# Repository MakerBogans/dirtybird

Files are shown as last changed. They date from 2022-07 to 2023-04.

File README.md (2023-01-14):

# The DirtyBird toolhead

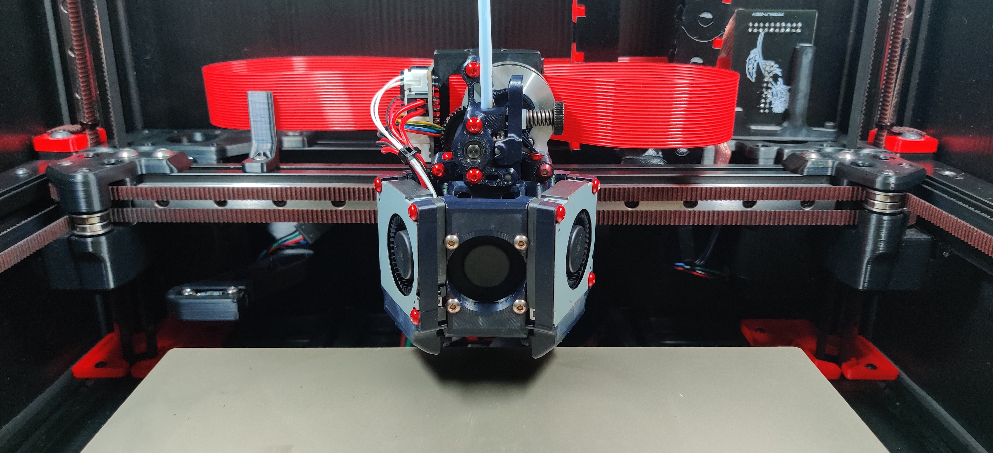
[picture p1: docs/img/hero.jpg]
DirtyBird Toolhead


Developed as the successor of the Frankensherpa toolhead.

Like its predecessor, DirtyBird is designed to:

- Be lightweight, allowing greater acceleration and potentially improved resonance
- Have excellent cooling performance, with dual blower fans to improve overhang performance with many materials (including PLA)
- Have fans that are mounted low on the toolhead (cf. Afterburner) to improve resonance
- Allow for easy maintenance of the extruder
- Use a simplified carriage with integrated magprobe support
- Remain compatible with stock Voron (and Ramalama) idlers
- Support Roadkill-based chainless toolhead boards

Currently, DirtyBird supports the following extruders (and more via usermods):

- LGX mini
- Sherpa mini
- Sherpa micro

And the following hotends:

- Dragon
- NF Crazy
- Rapido (HF only, UHF not supported yet)

### BOM

[See BOM](./docs//bill-of-materials.md)

### Build Instructions

[See Build Instructions](./docs/build.md)

### Planned features

- MGN9 support (currently, the carriage fits MGN12 rails only)
- Filament sensor support (for Enraged Rabbit Carrot Feeder or other multi-material operation, under development)
- Integrated LED lighting (using Neopixels, currently experimental)
- Rapido hotend support (currently experimental)
- Cable chain mount (?)

### Known issues/to do list

- Potentially insufficient clearance between the Dragon core and the heater block of the Dragon hotend; as a result, the core may melt or otherwise cook, especially when using a silicone sock
  - Improvements have been made, but we are gathering feedback from real world usage.
- Rename files for version control/clarity (i.e. similar to Annex)
- Printed L/R marks for the fan ducts

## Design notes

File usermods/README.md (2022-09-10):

Contains usermods for the DirtyBird toolhead.

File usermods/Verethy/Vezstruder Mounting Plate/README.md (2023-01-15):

# Mod description

**Vz-Hextrudort Mounting Plate**

Mounting plate the attach the Vz-Hextrudort extruders.

Veztruder

# Status

Release

# Incompatibilities

None

# Update notes

2x M3x6 BHCS to secure from the bottom.

# Instructions

**Print settings**

The STL is correctly oriented, do not change orientation

**Additional hardware**

2x M3x6 BHCS

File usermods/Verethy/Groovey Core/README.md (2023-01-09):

# Mod description

**Groovey Core**

Adds a new core to allow groove mount hotends to be mounted to the DB

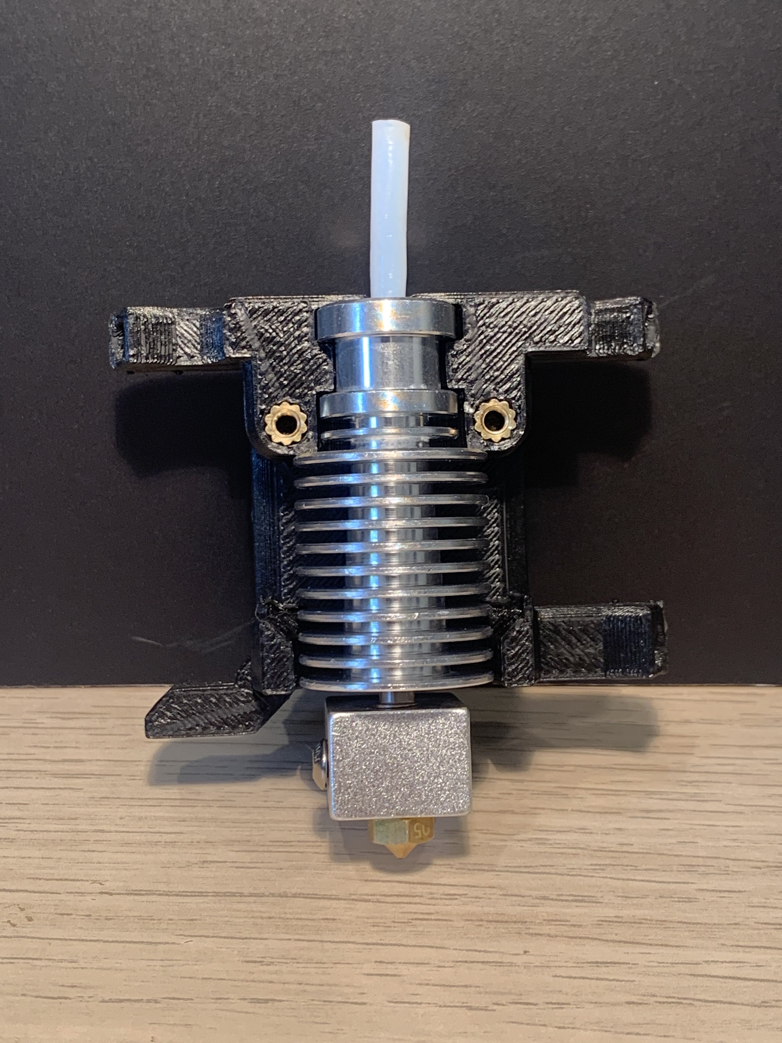
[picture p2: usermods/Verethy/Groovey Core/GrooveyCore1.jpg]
Groovey core

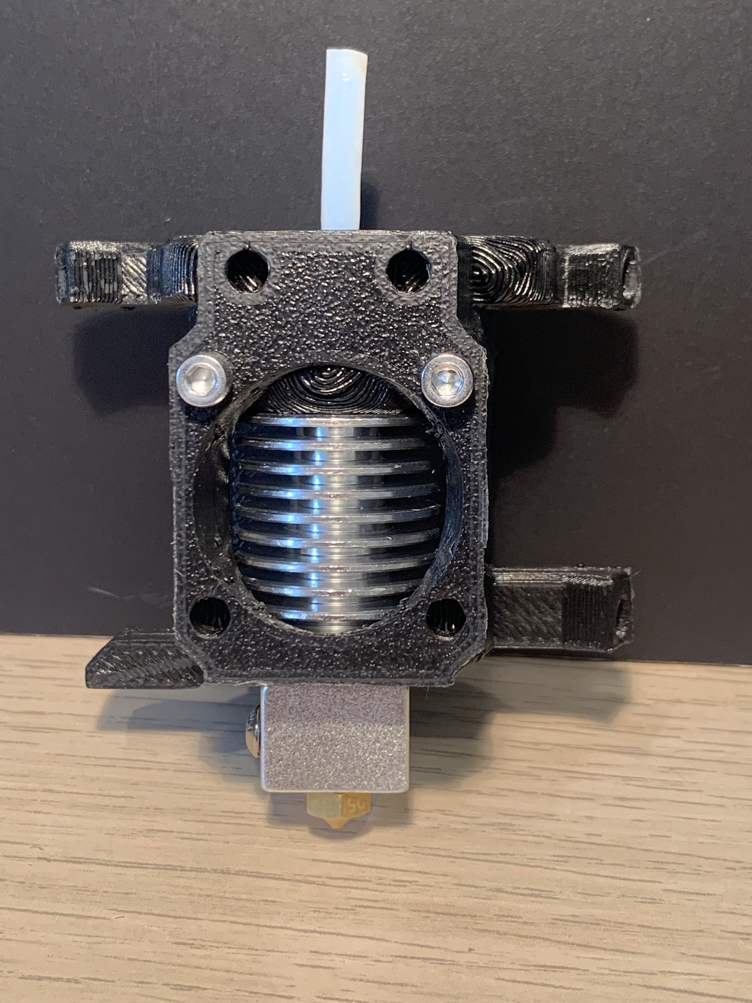
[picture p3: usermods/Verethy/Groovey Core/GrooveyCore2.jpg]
Groovey core

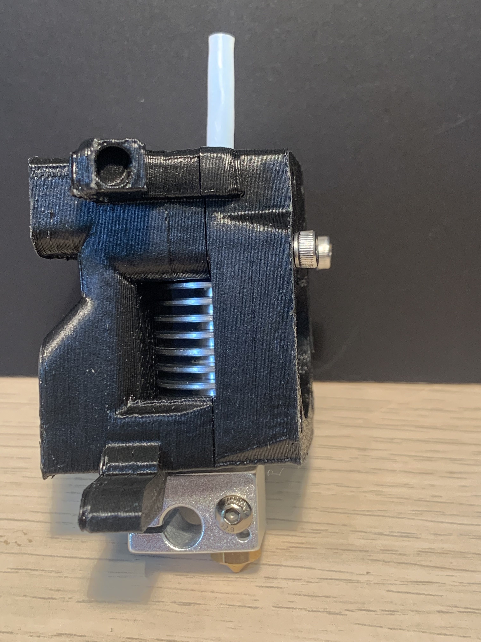
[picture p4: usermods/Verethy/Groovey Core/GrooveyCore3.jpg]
Groovey core


# Status

Release

# Incompatibilities

Sherpa Micro

# Update notes

Compatible with Dragon/Crazy ducts.
Replace the top 2 hotend fan screws with 2 M3x35mm BHCS

# Instructions

**Print settings**

The STL is correctly oriented, do not change orientation

**Additional hardware**

2x M3x35 BHCS

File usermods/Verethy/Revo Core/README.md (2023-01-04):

# Mod description

**Revo Core**

Adds a new core to allow Revo hotends to be mounted to the DB

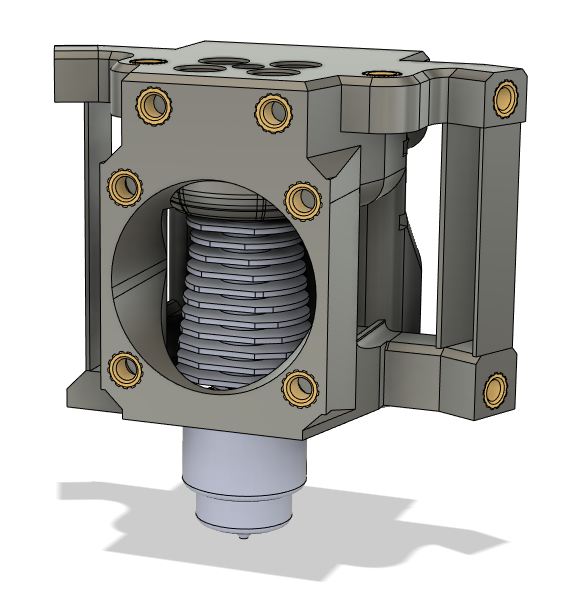
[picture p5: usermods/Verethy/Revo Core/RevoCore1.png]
Revo core


# Status

Release

# Incompatibilities

None

# Update notes

Compatible with Dragon/Crazy ducts.
Bowden length: 22.4 to top of core.

# Instructions

**Print settings**

The STL is correctly oriented, do not change orientation

**Additional hardware**

4x M3x8 SHCS

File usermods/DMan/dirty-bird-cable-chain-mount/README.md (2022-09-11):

# Dirty Bird Cable Chain Mount

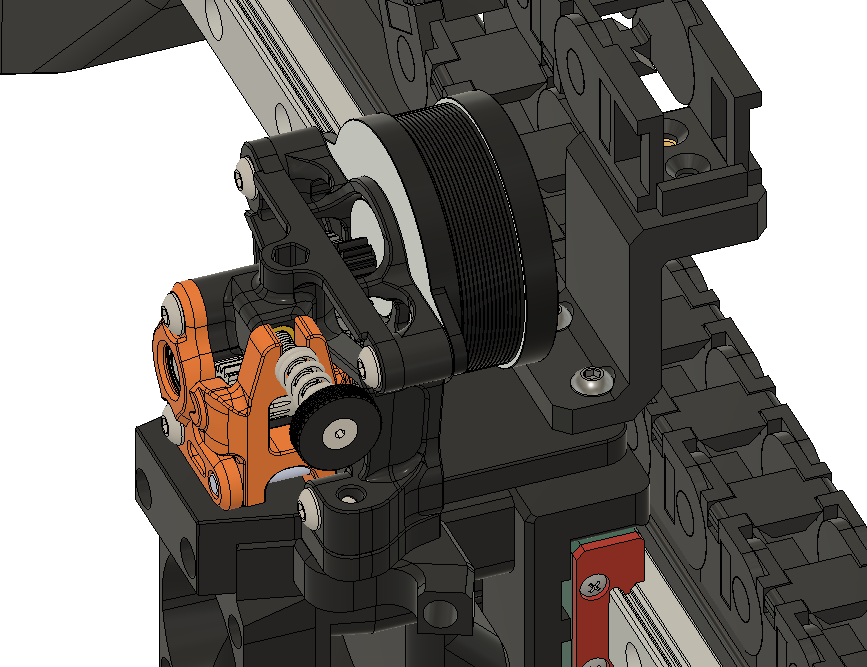
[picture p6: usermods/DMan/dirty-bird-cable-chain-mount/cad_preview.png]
Cable Chain Mount


## Status

I've got this on my V2.4 350 mm, and it works well!

## How to

Print on its side, no supports. 3x M3 inserts and BHCS screws to hold the chain in place, and 2x M3x12 BHCS/SHCS to hold the mount to the X carriage.

Note I'm using the Mini Sherpa mount. You might need to adjust the height by 4 mm if you are not using this little adapter!

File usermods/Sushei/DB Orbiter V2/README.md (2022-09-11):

Please note:
This mount cannot be used with the roadkill long PCB.

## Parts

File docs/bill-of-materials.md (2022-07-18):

# DirtyBird BOM

Exact fastener counts may differ slightly based on your configuration.

Purchasing spares is highly recommended.

For other projects that are used in DirtyBird (e.g. Klicky probe) refer to their respective documentation pages for an up-to-date BOM.

### Essential Fasteners

| Item | Quantity | Notes |
| :---: | :---: | :---: |
| Brass M3x4x5 Threaded Inserts | 20 | |
| M3x8 SHCS | 4 | |
| M3x12 SHCS | 3 | |
| M3x14 SHCS | 4 | |
| M3x16 SHCS | 3 | |
| M3x20 SHCS | 8 | |
| M3x6 BHCS | 2 | |
| M3x12 BHCS | 6 | |
| M3x20 BHCS | 4 | |
| M2.5 SHCS | 4 | Mounting bolts for your hotend (e.g. 10 mm bolts for Dragon hotends) |
| M3 SHCS/BHCS | 2 |  Mounting bolts for your extruder (e.g. M3x10 SHCS for Sherpa mini)  |

_BHCS button-head cap screw, SHCS socket-head cap screw_

### Fans

| Item | Quantity | Notes |
| :---: | :---: | :---: |
| Delta 4510 Blower Fan (BFB04512HHA-C) | 2 | |
| 3010 Hotend Cooling Fan | 1 | Airflow must be higher than 4 CFM |

### Other

| Item | Quantity | Notes |
| :---: | :---: | :---: |
| Extruder | 1 | Sherpa Mini, Sherpa Micro and LGX lite are currently supported |
| Hotend | 1 | Dragon & NF Crazy currently supported. Rapido support planned  |
| Bed Levelling Probe | 1 | Native support for Klicky. Euclid support in UserMod. |
| 6x3 Magnet | 3 | For Klicky mounting |
| 4mm OD, 2mm ID PTFE | 10cm | PTFE Liner between Extruder & Hotend |

### Optional Items

| Item | Quantity | Notes |
| :---: | :---: | :---: |
| Roadkill Longboi | 1 | Another board is recommended for terminating the ribbon cable, see Roadkill documentation for details |
| Roadkill Square | 1 | Support in UserMod. |
| Neopixel 5050 LEDs (on a 12.5mm diameter PCB) | 2 | TBC |
| Omron D2F Microswitch | 1 | For X endstop |

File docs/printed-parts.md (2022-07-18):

# DirtyBird Printed Parts

### Carriage

| Item | Filename | Notes |
| :---: | :---: | :---: |
| Klicky probe | Dirty Bird Klicky Carriage20 | |

### Hotend

Affects core and duct selection. Choose one set of files.

| Item | Filename | Notes |
| :---: | :---: | :---: |
|  Dragon  | DB Dragon Core | Available as two files (with or without supports) |
| |  Dragon Left Duct | |
| |  Dragon Right Duct  | |
| NF Crazy | DB Crazy Core | Available as two files (with or without supports) |
| | NF Crazy Left Duct  | |
| | NF Crazy Right Duct | |

### Extruder

Affects mount. Choose one.

| Item | Filename | Notes |
| :---: | :---: | :---: |
| Sherpa Mini  | Sherpa Mini Mount | |
| LGX Lite |  LGX Lite Mount | |
| Sherpa Micro |  [not required] | Note: stock cores will fit Sherpa micro extruders without a mount |

### Fan Brace

Choose one set.

| Item | Filename | Notes |
| :---: | :---: | :---: |
| One Piece | Fan Front Brace | Available as two files (with or without teeth) |
| Two Piece | Fan Front Brace 2 | Available as two files (the toothed insert can be printed separately with this version for ease of printing or for multicolour) |
| | Fan Front Brace 2 Piece Insert Blank | |

### Other

| Item | Filename | Notes |
| :---: | :---: | :---: |
| Cable Mount | Cable Mount | Routing for ribbon cables |
| | Cable Mount Spacer | Required if mounting plate isn't used |

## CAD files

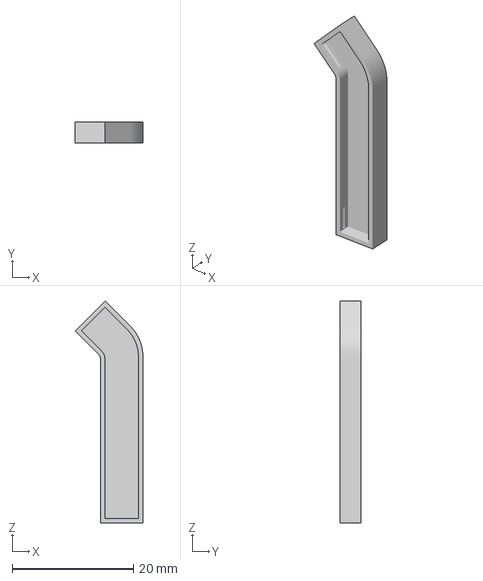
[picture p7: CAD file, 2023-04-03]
3mf/Cable Management/RKE Ribbon Mount Cap.3mf
11.2 x 3.50 x 36.6 mm

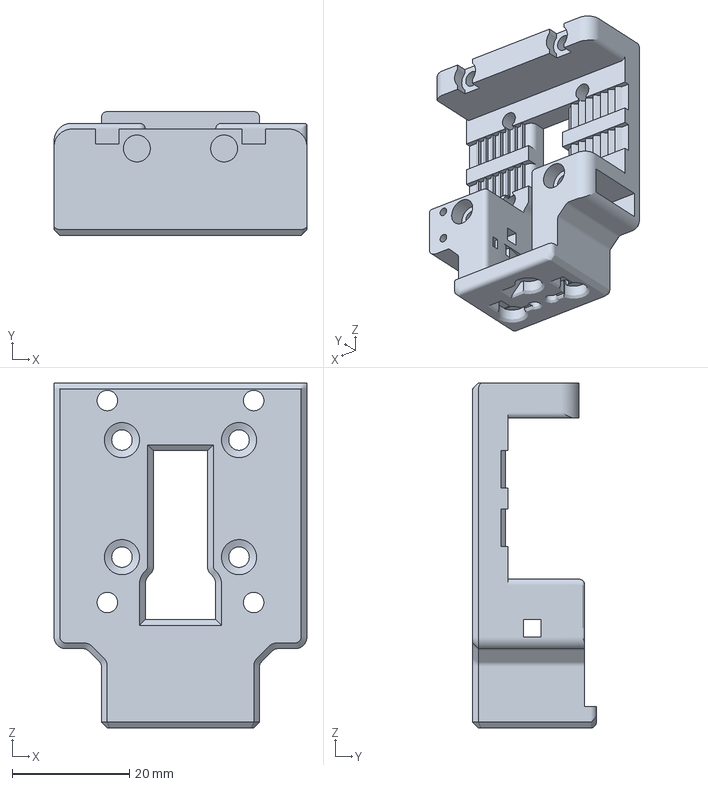
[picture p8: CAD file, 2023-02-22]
3mf/Carriage/DB Klicky Carriage JST.3mf
43.2 x 21.2 x 58.9 mm

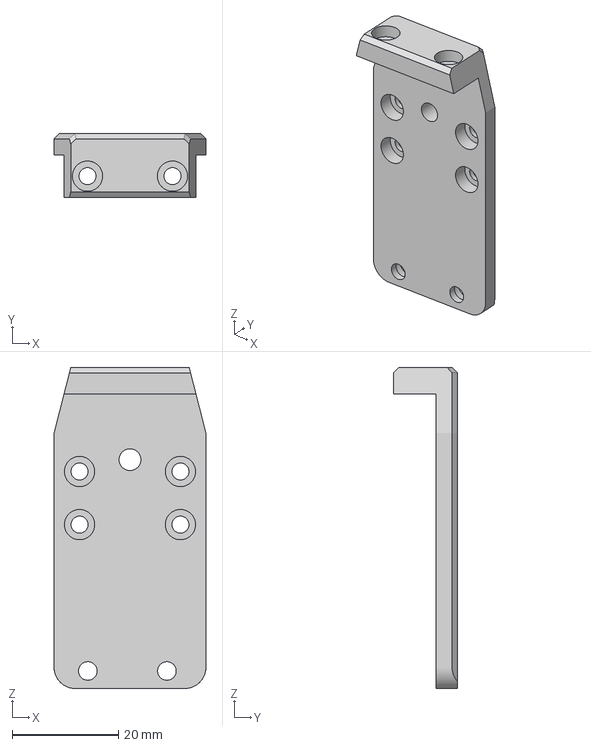
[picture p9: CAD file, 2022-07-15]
3mf/Extruder/DB - LGX Lite Mount V1.3mf
28.6 x 12.0 x 60.5 mm

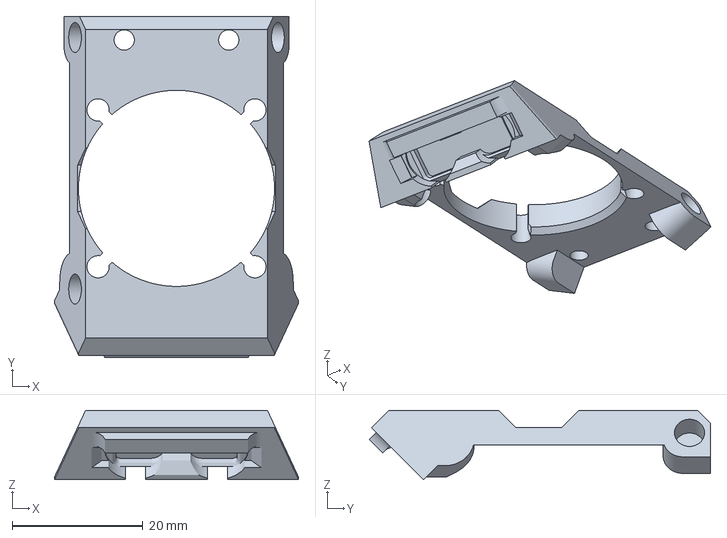
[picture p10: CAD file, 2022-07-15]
3mf/Hotend Cooling/DB Fan Front Brace V1.1.3mf
37.3 x 52.3 x 10.6 mm

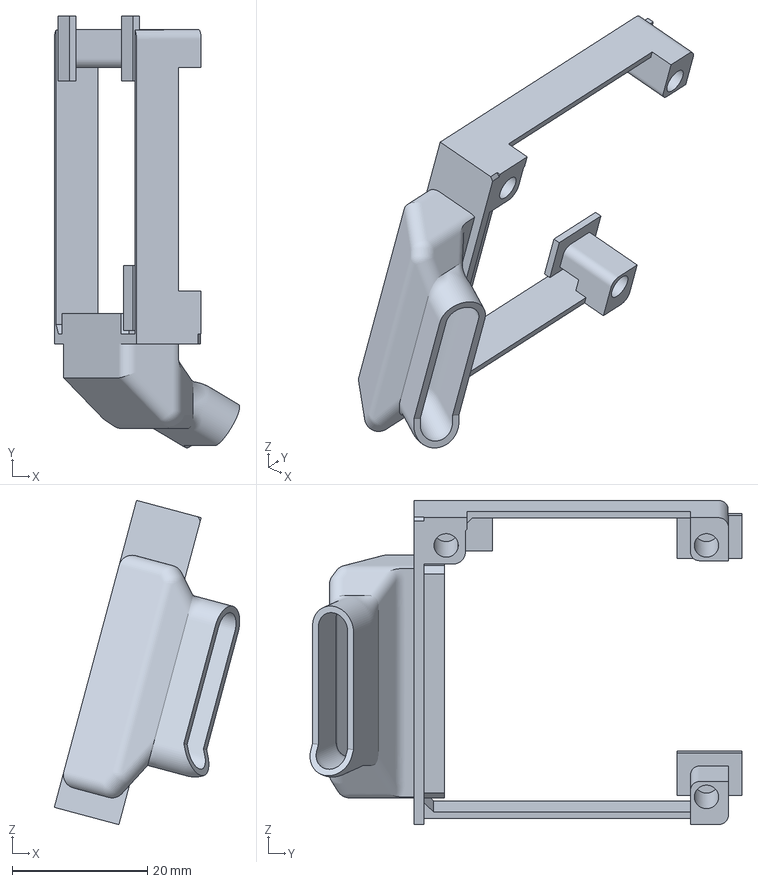
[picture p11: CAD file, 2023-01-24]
3mf/Part Cooling/Dragon - NF Crazy/Carpet Bmb Dragon Crazy Left New Fan.3mf
27.4 x 63.9 x 48.0 mm

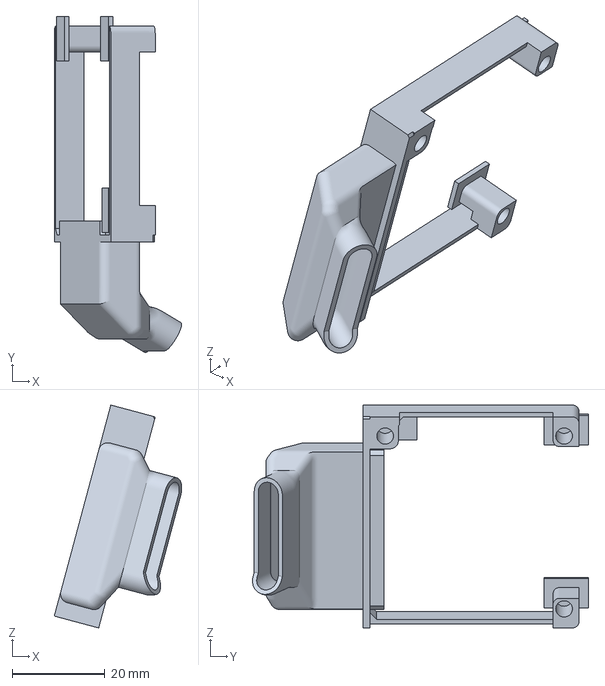
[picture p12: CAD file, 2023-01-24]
3mf/Part Cooling/Rapido HF/Carpert Bmb Rapido Left New Fan.3mf
27.4 x 72.3 x 48.0 mm

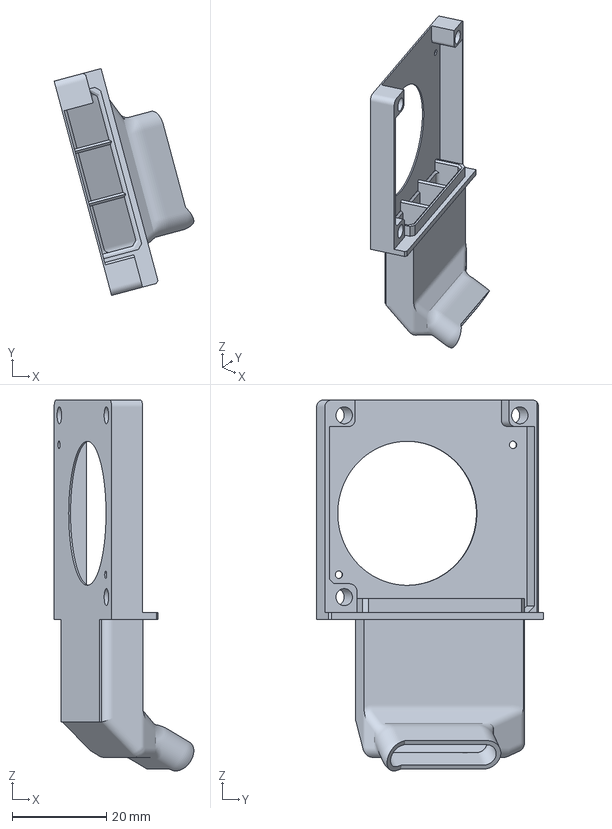
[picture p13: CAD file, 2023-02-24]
3mf/Part Cooling/Rapido UHF/Carpert Bmb Rapido UHF Right With Cover.3mf
29.6 x 48.1 x 78.6 mm

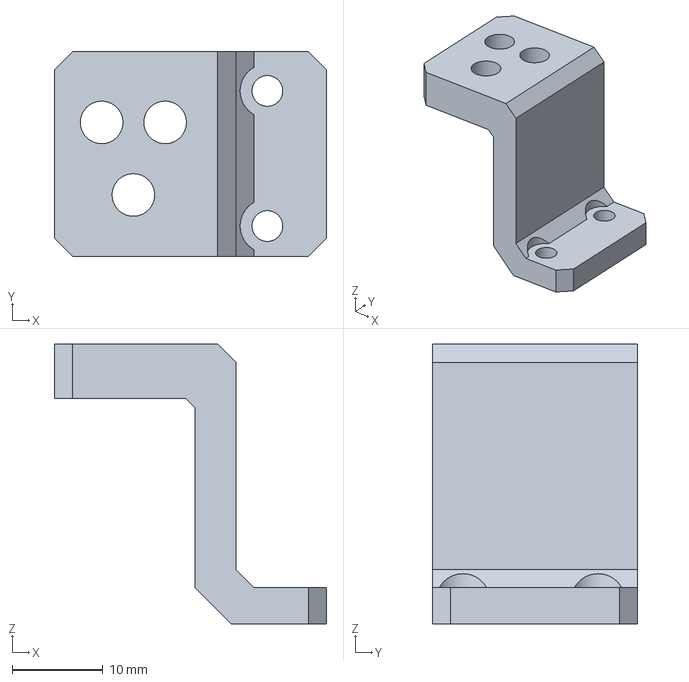
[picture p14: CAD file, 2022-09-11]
usermods/DMan/dirty-bird-cable-chain-mount/dirty-bird-chain-mount.3mf
30.0 x 22.6 x 30.8 mm

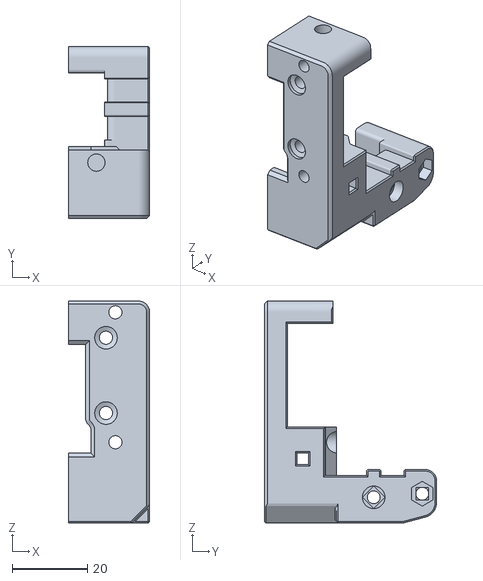
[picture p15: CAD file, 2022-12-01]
usermods/Gruesome/Euclid for SW/DB SW right.stl
21.6 x 45.7 x 58.9

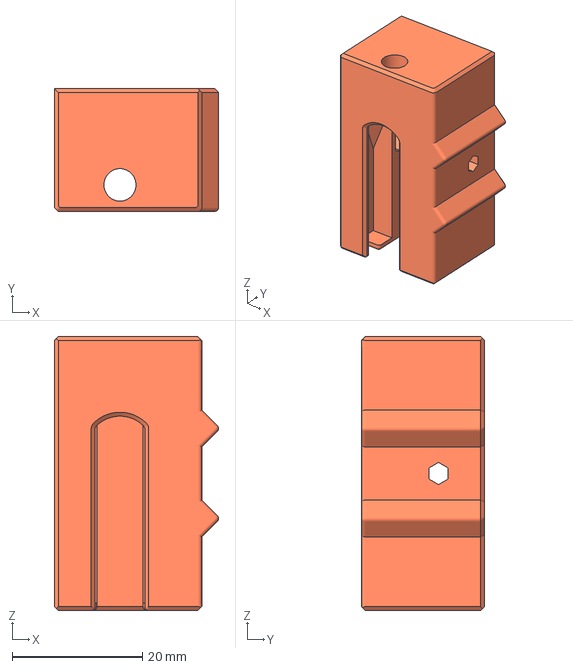
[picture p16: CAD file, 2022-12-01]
usermods/Gruesome/Euclid for SW/docks/dock bed mount.3mf
25.2 x 18.8 x 42.0 mm

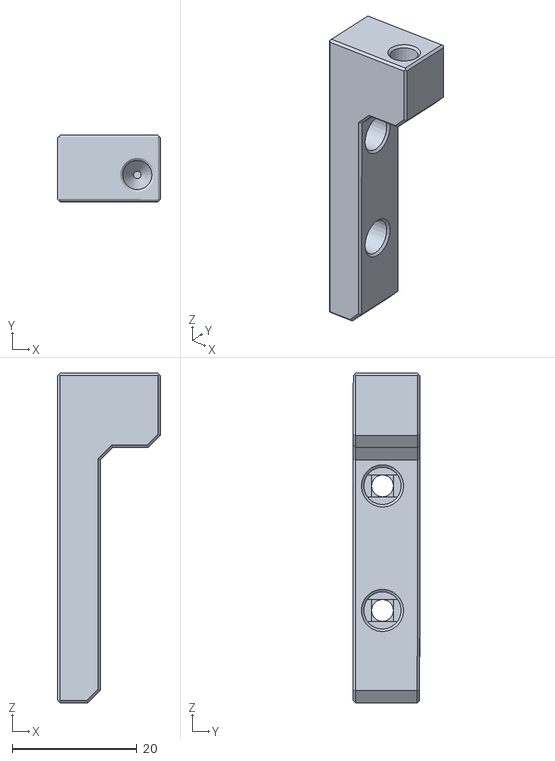
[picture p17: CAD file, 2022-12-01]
usermods/Gruesome/Euclid for SW/docks/euclid servo mounts/Servo_dock_mount_right.stl
16.5 x 10.7 x 53.0

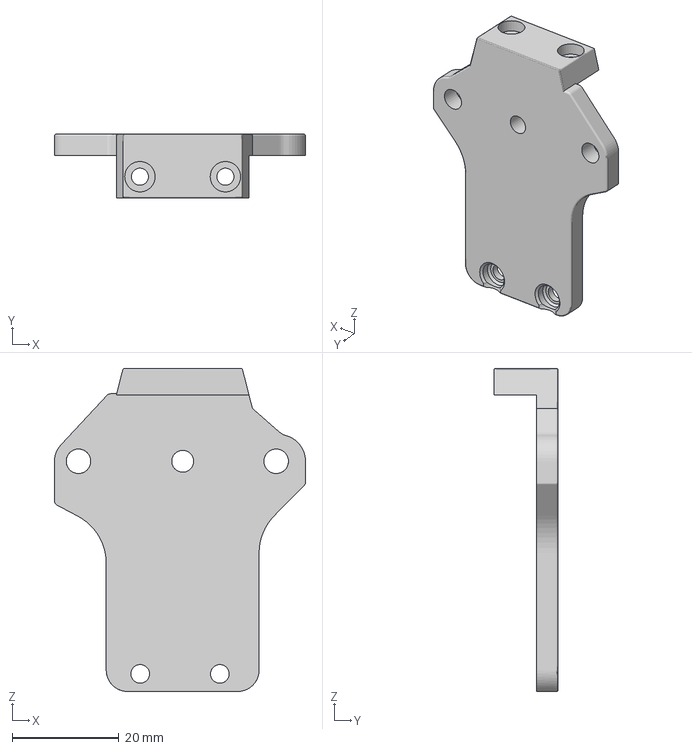
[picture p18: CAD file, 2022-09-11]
usermods/Sushei/DB Orbiter V2/Dirty_Bird_-_Orbiter_v2_Mount.3mf
47.0 x 12.0 x 60.5 mm

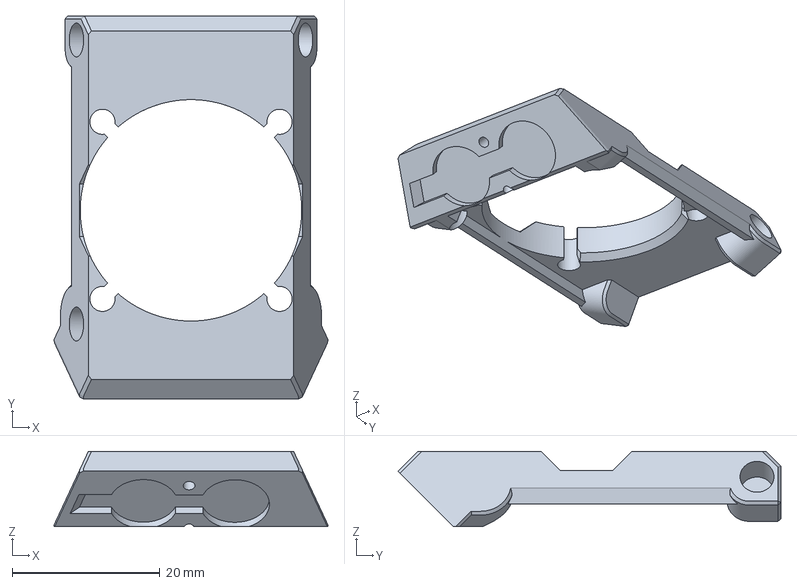
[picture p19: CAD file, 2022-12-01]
usermods/Sushei/Sushei's Version/3mf/[Rev5] Fan Brace.3mf
37.1 x 51.9 x 10.2 mm

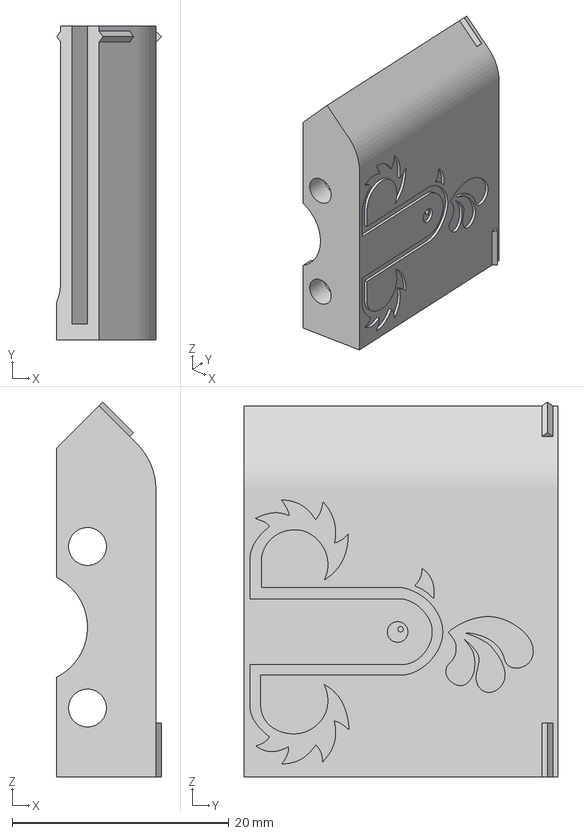
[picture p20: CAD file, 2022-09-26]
usermods/Verethy/Cable Holder for Sheath/Cable Holder Body Sheath.3mf
9.67 x 29.0 x 34.6 mm

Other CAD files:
usermods/Verethy/Groovey Core/Grovey Core Front V1.3mf
usermods/Verethy/Revo Core/Dirty Bird - Revo Core V1.2.3mf
usermods/Verethy/Vezstruder Mounting Plate/Dirty Bird - Vezstruder Mounting Plate v2.3mf
3mf/Cable Management/RKE Ribbon Mount Body.3mf
3mf/Cable Management/DB - Cable Mount Spacer V1.3mf
3mf/Carriage/DB Euclid Carriage.3mf
3mf/Carriage/DB Euclid Dock Gantry Mount.3mf
3mf/Carriage/DB Klicky Carriage V1.3mf
3mf/Carriage/DB_Euclid_Carriage_JST.3mf
3mf/Carriage/DB_Eureka_Carriage_JST.3mf
3mf/Core/DB Crazy Core Square Nut.3mf
3mf/Core/DB Crazy Core V1.3mf
3mf/Core/DB Dragon-Rapido Core Square Nut.3mf
3mf/Core/DB Dragon-Rapido Core V1.1.3mf
3mf/Extruder/DB - Sherpa Mini Mount V1.3mf
3mf/Hotend Cooling/DB Fan Insert V1.1.3mf
3mf/Part Cooling/Dragon - NF Crazy/Carpet Bmb Dragon Crazy Left v1.3mf
3mf/Part Cooling/Dragon - NF Crazy/Carpet Bmb Dragon Crazy Right New Fan.3mf
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

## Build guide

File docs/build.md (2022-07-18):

# DirtyBird Build Instructions

See [printed parts](./printed-parts.md) for a list of required 3d printed parts.

### Step 1: Preparing Parts

Remove any supports (e.g. the supports included in the pre-supported core variants)

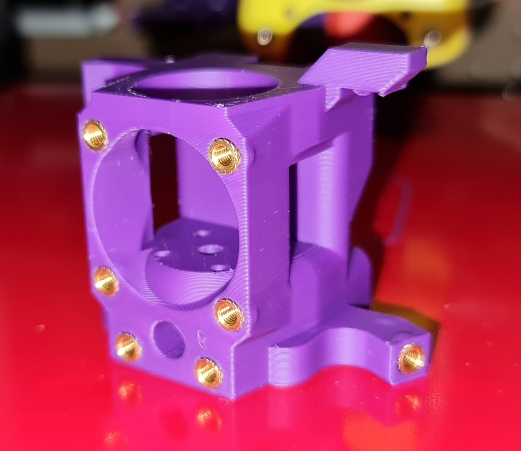
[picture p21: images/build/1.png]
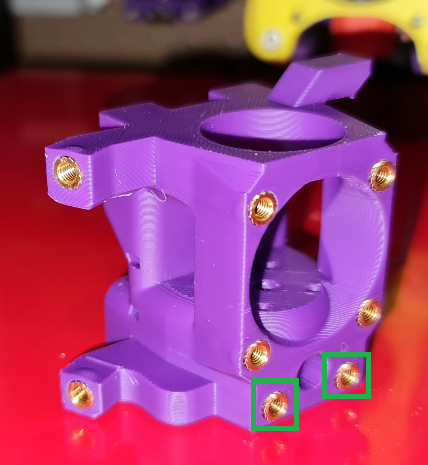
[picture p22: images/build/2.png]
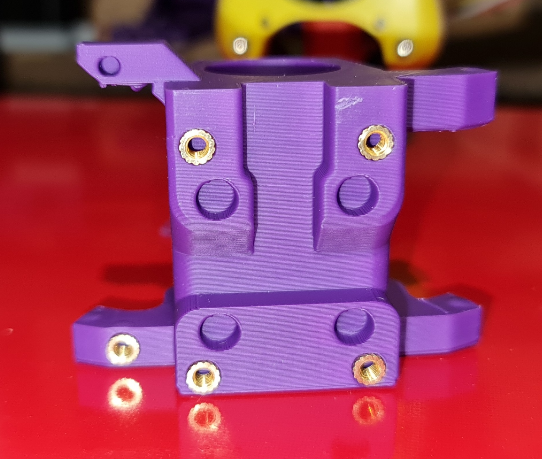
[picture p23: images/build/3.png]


Core heatset inserts part 1; inserts shown in green squares are only required for toolheads using a mounting plate (i.e. do not install these if you are using a Sherpa micro)

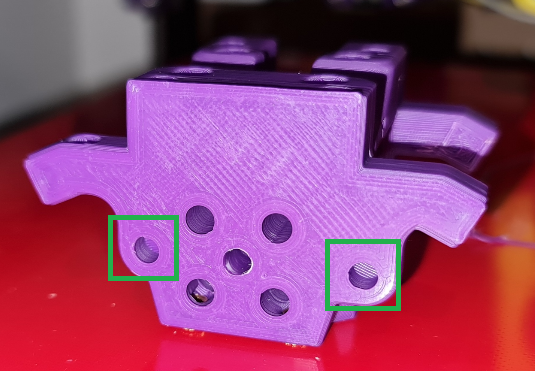
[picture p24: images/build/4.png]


Core heatset inserts part 2; add inserts shown in the green squares if you are using a Sherpa micro

Note: for release v1 (or earlier versions), you may need to drill out the PTFE tube path with a 4 mm bit, otherwise it may be difficult to push the tube through.

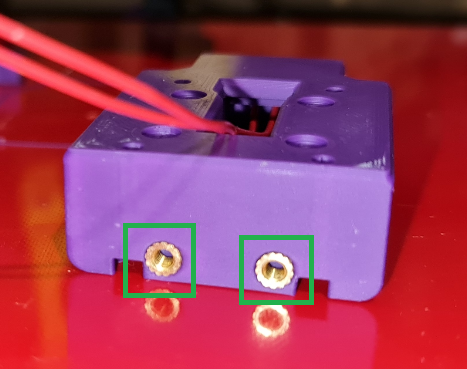
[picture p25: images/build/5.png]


Carriage heatset inserts (required for all extruders, the cable guide will attach to these)

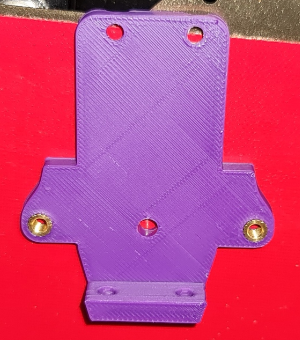
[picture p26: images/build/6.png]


If you are using a mounting plate for the Sherpa mini\BMG extruder, add two heatset inserts as shown

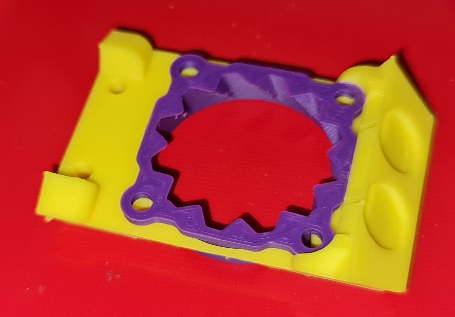
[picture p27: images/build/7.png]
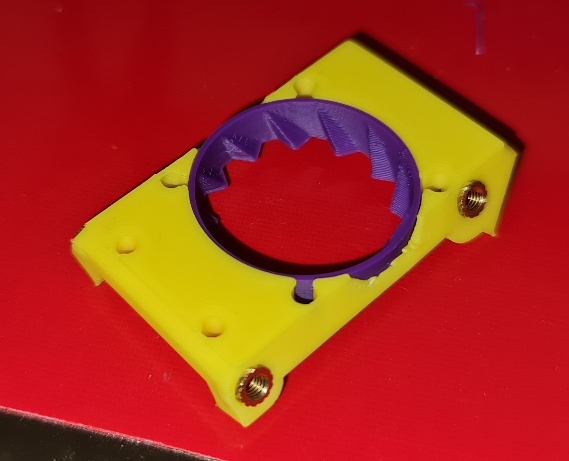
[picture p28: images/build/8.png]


If you are using a two-piece fan brace, carefully combine the two pieces BEFORE proceeding to heatset insertion. The toothed (or blank) insert will impart much needed rigidity to the brace.

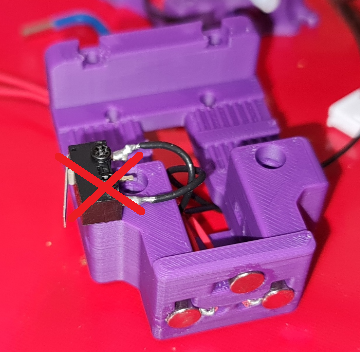
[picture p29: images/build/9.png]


- Press three 6x3 magnets into the carriage. Refer to Klicky documentation regarding the polarity of these magnets.
- Pressing the magnets against a flat surface is recommended to keep the surface as flat as possible; this improves the reliability of the Klicky probe.
- The carriage may slightly crack during this process, use cyanoacrylate glue to make repairs and to secure the magnets.
- You may attach the X endstop to the carriage at this stage, or leave it off for easier assembly in a future step.

### Step 2: Core Assembly

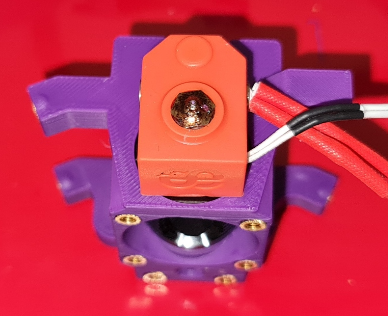
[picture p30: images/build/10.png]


- Insert your hotend into the core. For Dragon hotends, take note of the nozzle/block orientation. The nozzle should be closer to the front (i.e closer to the 3010 cooling fan).
- Use the appropriate bolts to secure the hotend to the core (e.g. M2.5x10 SHCS for Dragon hotends)

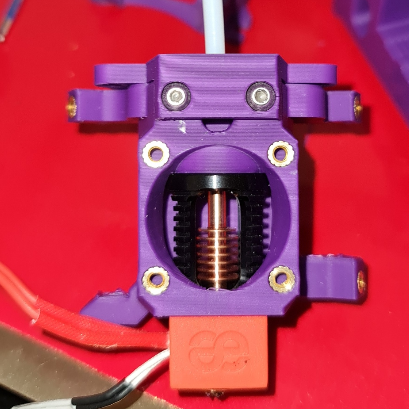
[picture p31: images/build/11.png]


- Use two M3x6 BHCS to secure the mounting plate to the core (if you require a mounting plate). Do not overtorque!
- Push through a 4mm OD PTFE tube through the top until it contacts the hotend.
- The recommended tube length is ~30 mm for a Dragon hotend and Sherpa mini extruder; you may have to find the appropriate length for your chosen combination of hotend and extruder.

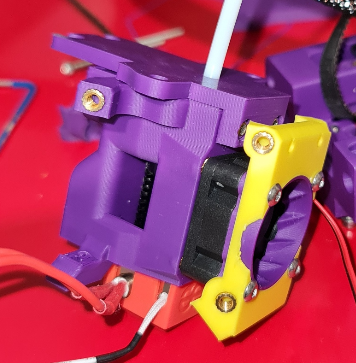
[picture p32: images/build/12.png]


- Attach the 3010 hotend cooling fan and fan brace to the core using four M3x20 BHCS, as shown
- The fan should be drawing air towards the hotend (i.e. the sticker should not be visible from the front)

### Step 3: Fan Assembly

Slide the fan ducts over the 4510 blower fans. Then, secure the fan assemblies to the core and fan brace using 3 M3x12 BHCS per duct, as shown below.

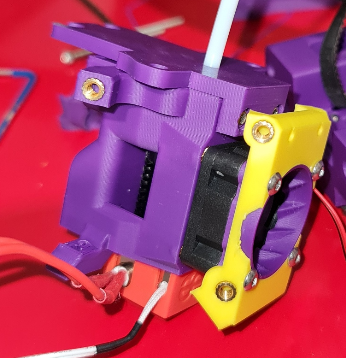
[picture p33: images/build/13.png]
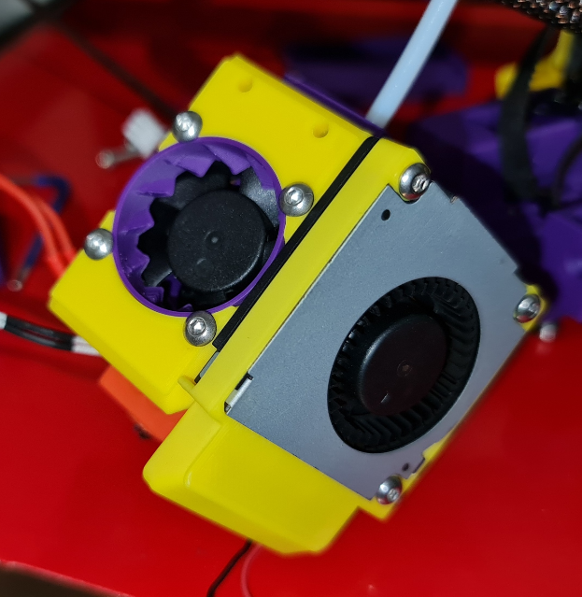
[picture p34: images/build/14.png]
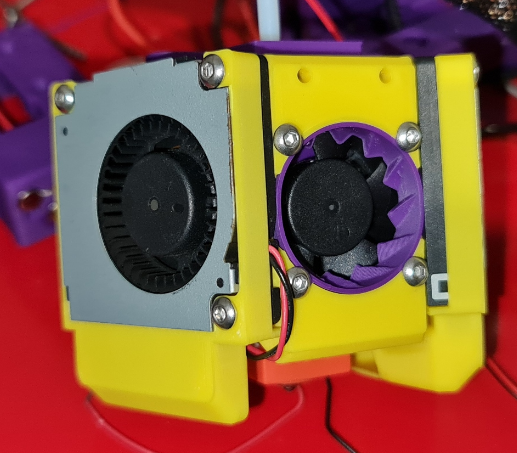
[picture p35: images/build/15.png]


### Step 4: Mounting the extruder

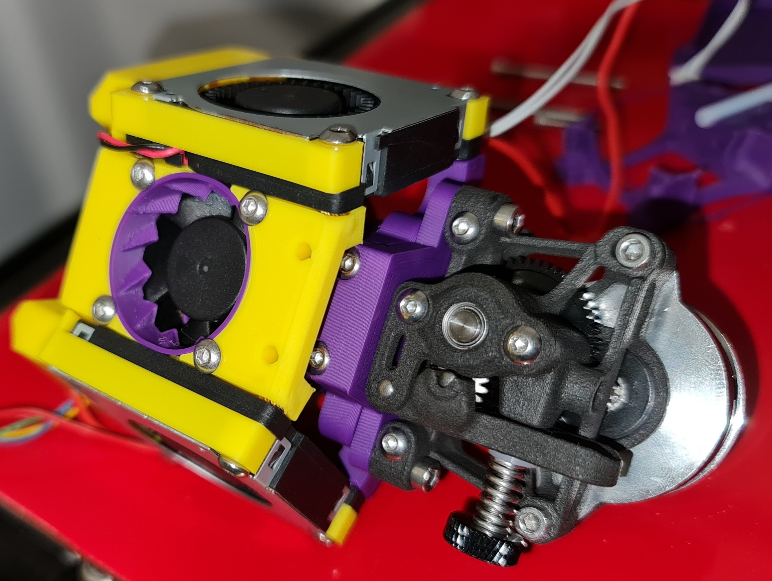
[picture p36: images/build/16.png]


- Use two mounting bolts (e.g. M3x10 BHCS for the Sherpa mini extruder) to secure the extruder to the mounting plate.
- Do not forget to include a PTFE tube between the extruder and hotend!

### Step 5: Carriage Assembly

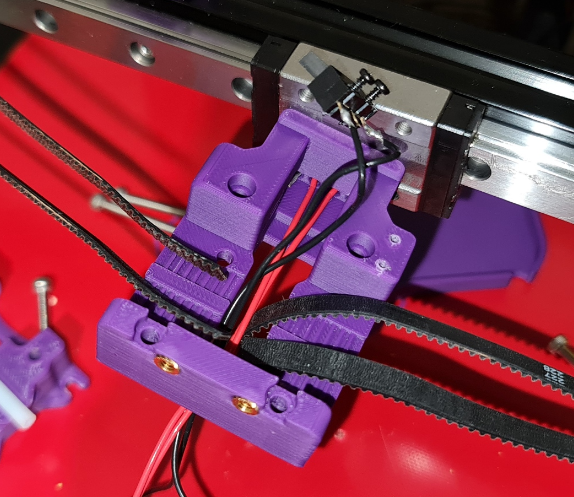
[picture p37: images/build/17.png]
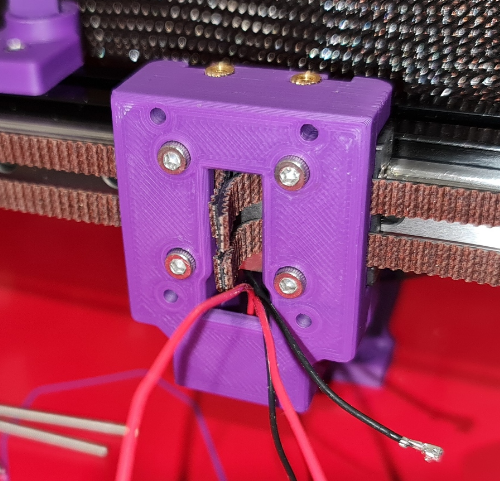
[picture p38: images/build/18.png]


- As with the stock Voron carriage, the belts are secured between the carriage and the block. Thread the belts and Klicky-related wires (red wires in this diagram) through the hole, as shown.
- If you are using an X endstop microswitch, you can either attach the microswitch or keep it off for easier assembly. However, ensure that the wires are pushed through the cavity, as shown (black wires).
- Use four M3x8 SHCS to attach the carriage to the block. The heads will sit proud (sticking out), which will help with alignment during final assembly. The exact depth of these bolts isn’t essential, but ensure the carriage is secured tightly against the rail block to reduce unwanted play.

### Step 6: Final Assembly

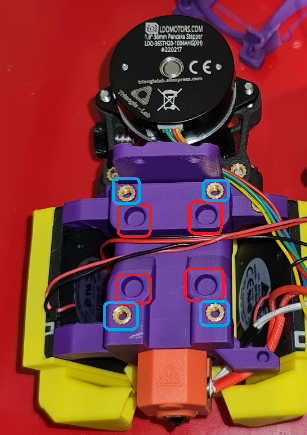
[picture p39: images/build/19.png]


- Before proceeding, take note of the channel dedicated to wiring (black and red wires shown here).
- Also, the holes indicated by red boxes are to help with alignment (as indicated in the previous step).
- The heatset inserts within the blue boxes are used to attach the toolhead to the carriage.

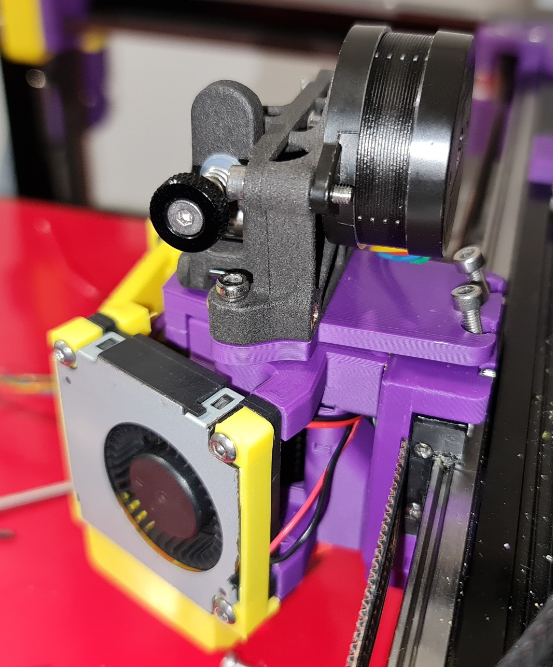
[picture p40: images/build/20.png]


- Line up the toolhead and carriage and use four M3x20 SHCS to attach the toolhead.
- If you are using a mounting plate, use two M3x8 SHCS to secure it to the carriage.
- You may now attach the X endstop microswitch to the carriage (if not already installed).
- If the microswitch is already installed on the carriage, you will need to slide the carriage on from the side of the block, as the switch will prevent the carriage being applied ‘head on’

For wiring instructions, consult Roadkill longboi documentation.

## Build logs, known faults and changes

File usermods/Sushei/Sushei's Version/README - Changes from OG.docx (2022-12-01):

This is effectively Sneeky_Pete’s release with some changes.

Core:

- Use (+clearance) version if standard core is too tight around the cold end.
- Use (+2mmY) for Trident with z endstop pin. Moves nozzle +2mm in Y to reach the pin. *you will lose 1mm in X travel
- Sherpa Mini only, adapter plate deleted.
- Extruder sits 4mm lower (same as Micro always has).
- 2mm offset, 1.6mm deep recess around the heat-block, hopefully avoiding a melty core.
- Longboi moved 2mm to the rear (+Y) - for clearance between IDC pins and lowered extruder motor.
- Front facing heater screw terminal. *must use my ducts
- Heatsert holes for 3010 fan extended by conical m3x1.6 cut for iron tips.
- Anchor for heater wire between heat-block and core.

Ribbon Cable Mount

- Body thickened at the base. Otherwise use OG mount body +spacer.

Fan ducts (dragon only), inspired by Bioshank’s work:

- Dragon Duct Left/Right are 1mm above the nozzle
- Dragon Duct Left/Right (Short Cover) are 2mm above the nozzle and replace stock fan shields.
- Compatible with Sneeky_Pete’s core.
- Airflow clears the block and nozzle body, and should be more direct.

Front fan brace:

- Adjusted for LED wiring and mount.
- Vertical ribs.

LED Mount:

- For 2x neopixel button LEDs. *must use my fan brace
- Need 1 m2x10mm(top) and 1 m2x6mm (bottom, just cut a 10mm one) screw.
- Neopixel wires exit from the left (-X) side.

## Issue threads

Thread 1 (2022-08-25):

Mod for Bontech LGX lite, Mellow's NF crazy hotend and umbilical cord

thomasschoenfeld, 2022-08-25:
I took the initial release from 18.July 2022 and modified it for my purposes. I am using a Bondtech LGX lite, Mellows NF crazy hotend with that bigger heat block, umbilical cord, no LEDs in the toolhead.

Modifications:
- Core modifications:
    - moved the inside deck, where the top of the hotend touches the core, up 9 mm. For one the inside lower deck seemed to thick. Secondly the bigger heat block would make the nozzle sit lower than need, as this wastes overall max printing height by that amount (not a big deal, but none the less) and also requires the part cooling fan ducts to be bigger. With the 9mm higher Hotend, the normal height of a normal mosquito style hotend is achieved and one can use the smaller dan ducts. This saves weight overall in the toolhead, which is also a plus.
    - modified the inside geometry, to make more room for the heat block, to be as further away, reducing the risk of melting the core
    - changed / deleted some of the whole-outs to work with the Bondtech LGX Lite.
    - had to design a adapter plate for the Bondtech LGX Lite as well; added to inserts on the top front, while using the inserts in the carrier to mount the adapter
    - designed a mount for umbilical cord
    - deleted the parts required for the PCB (as I don’t need them; could easily be added again)
    - designed a insert mount an the left side, to attach the “hotend pincher”
    - designed an pincher / pressing part, which presses agains the cooling body of the hotend, to fix it better
    - multiple fine-tuning changes to improve spacings, weight, stability and printability
- Fan front brace modifications:
    - losing the fan insert completely. I really don’t see the point of it. The air flow winglets don’t do much in such a small form factor. Reducing the weight (only slightly, because….)
    - used the 2mm depth gained by loosing the fan insert do thicken / strengthen the core a bit the core a bit. Was necessary anyway, because the part cooling brace position can not really be changed, unless changing a lot of the angles etc.
    - loosing the LED slot
    - moved the fan and screw whole-outs up, to better fit the new hotend position
- ADLX (temporary) mount, which can be attached to the fan front brace
- Carrier > changes the bottom geometry to lift up the klicky mount magnets, to now fit with the raised hotend, while using a unklicky BFP.

[Uploading Dirty Bird - Beta Release V1.1 mod by TS v32.f3d.zip…]()

SomeoneWeird, 2022-09-07:
Hey @thomasschoenfeld looks like your upload didn't work properly!

thomasschoenfeld, 2022-09-07:
[DirtyDird_mod_TS_v38.f3d.zip](https://github.com/MakerBogans/dirtybird/files/9509029/DirtyDird_mod_TS_v38.f3d.zip)
try this one.... updated / lastest version of my model

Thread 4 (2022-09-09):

Orbiter 2, Can Board?

Tuerlich86, 2022-09-09:
Hi, Do you plan to support the Orbiter 2 and a 42 can board?

SomeoneWeird, 2022-09-11:
Hey @Tuerlich86 - we just pushed a mod for Orbiter 2 support. The way the motor is mounted means that you can't use the recommended Roadkill Longboi PCB though :)

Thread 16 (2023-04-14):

Rapido HF  - klicky clearance

Vercanti, 2023-04-14:
Hello! I printed the core for a rapido, using the mounts for klicky there seems to be a clearance issue. Is there a file for a longer base to accomodate the longer Rapido using Klicky?

legend069, 2023-04-14:
> Hello! I printed the core for a rapido, using the mounts for klicky there seems to be a clearance issue. Is there a file for a longer base to accomodate the longer Rapido using Klicky?

Can you please elaborate
Where is the clearance issue ?
(Photos help )

Verethy-0127, 2023-04-14:
Do you have the correct probe spacer printed for the Rapido?

https://github.com/jlas1/Klicky-Probe/blob/main/Probes/KlickyProbe/STL/Switch_extender.stl

Vercanti, 2023-04-14:
I'm going to print it and give it a go! Thank you!

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

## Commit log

2022-07-07 Add Rapido to supported hotends
2022-07-15 Remove STLs, Add 3mf & CAD files
    [Cable Holder Body.stl, Cable Holder Cap.stl, Cable Mount Spacer.stl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]
2022-09-09 Moved to correct folder
    [DB Revo Core.stl]
2022-09-09 Added Revo Voron core
    [DB Revo Core.stl]
2022-09-11 Fixing Revo Core, adding Sushei Orbiter v2 mount (#5)
    * Delete DB Revo Core.stl
    * Create asd
    * Fixed Revo core
    * Add Orbiter v2 mount
    * Add Orbiter V2 mount
    * Delete asd
    * Update Revo Core
    * Update README.md
    [DB Revo Core.stl, Dirty_Bird_-_Orbiter_v2_Mount.3mf]
2022-09-11 Adding DB chain mount to dirtybird repo (#6)
    [dirty-bird-chain-mount.3mf]
2022-09-26 Expanded cable holder to accomodate cable sheath. (#7)
    [Cable Holder Body Sheath.3mf]
2022-12-01 Added Euclid carriage & gdrive usermods (#8)
    * Added Euclid Carriage
    -Added Euclid carriage
    -Merged usermods from gdrive
    -Some folder cleanup
    * Added Bob ducts with covers
    Added Bob ducts with covers
    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
    [Cable Holder Body Sheath.3mf, DB Carriage V1.3mf, DB Euclid Carriage.3mf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]
2023-01-04 Add RKE Ribbon Mount
    Add RKE Ribbon Mount
    [RKE Ribbon Mount Body.3mf]
2023-01-04 Updated Revo core files
    Updated Revo core files
    [DB Revo Core.stl, Dirty Bird - Revo Core V1.2.3mf, Dirty Bird - Revo Core V1.2.f3z]
2023-01-09 Add groovey core
    Add groovey core
    [Groovey Core Rear V1.3mf, Groovey Core V1.f3z, Grovey Core Front V1.3mf]
2023-01-15 Add Vezstruder mounting plate
    Add Vezstruder mounting plate
    [Dirty Bird - Vezstruder Mounting Plate v2.3mf, Dirty Bird - Vezstruder Mounting Plate.f3d]
2023-01-24 Part cooling ducts for new generation 4510
    [Carpert Bmb Rapido Left New Fan.3mf, Carpert Bmb Rapido Right New Fan.3mf, Carpet Bmb Dragon Crazy Left New Fan.3mf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]
2023-02-02 Create DB_Eureka_Carriage_JST.3mf
    Added Eureka carriage
    [DB_Eureka_Carriage_JST.3mf]
2023-02-02 Add CAD for Eureka JST carriage
    Add CAD for Eureka JST carriage
2023-02-03 Added Euclid JST carriage
    Added Euclid JST carriage
    [DB_Euclid_Carriage_JST.3mf]
2023-02-03 Add files via upload
    Modified version of original core to support use of square nuts instead of heatset inserts for mounting core to carriage
    [DB Dragon-Rapido Core Square Nut.3mf]
2023-02-03 Create DB Crazy Core Square Nut.3mf
    [DB Crazy Core Square Nut.3mf]
2023-02-22 Create DB Klicky Carriage JST.3mf
    [DB Klicky Carriage JST.3mf]
2023-02-24 Rapido UHF Carpet Bomb Ducts Uploaded
    [Carpert Bmb Rapido UHF Left With Cover.3mf, Carpert Bmb Rapido UHF Right With Cover.3mf]
2023-04-03 Add missing ribbon mounting cap
    [RKE Ribbon Mount Cap.3mf]
